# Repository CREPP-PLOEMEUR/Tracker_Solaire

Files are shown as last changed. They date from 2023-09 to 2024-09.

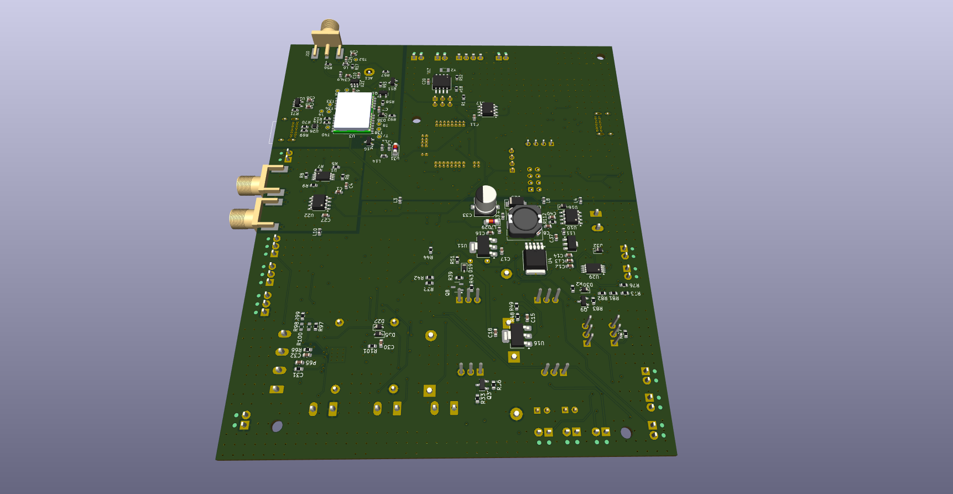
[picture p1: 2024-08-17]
Hardware/V2_CMS_4_Layers/Render/Bottom.png

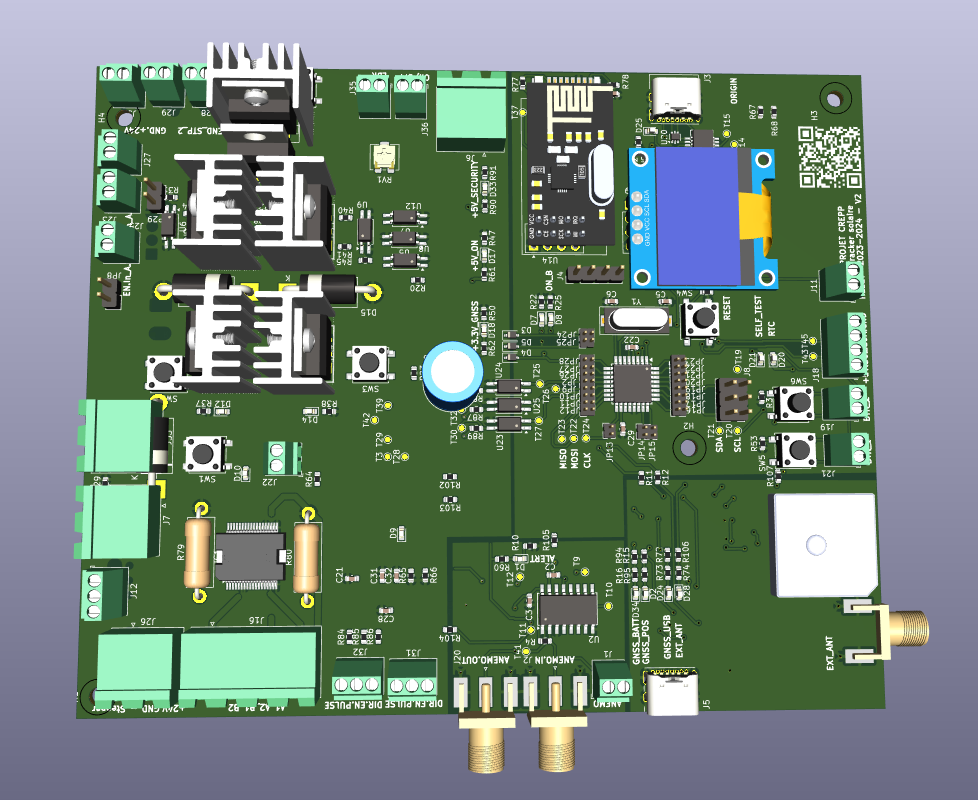
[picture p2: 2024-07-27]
Hardware/V2_CMS_4_Layers/img/img.png

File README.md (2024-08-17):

<!--# Tracker solaire -->
<!--+ 2023-2024 -->
<!--$ C++-->
<!--$ Freecad -->
<!--$ GPS -->
<!--% Ce projet vise à concevoir et construire un système de suivi solaire spécialement conçu pour maximiser l'efficacité de la capture d'énergie solaire à partir d'un panneau solaire. -->
 -->
# Projet de Tracker Solaire pour Panneau 1m x 1m60

Ce projet vise à concevoir et construire un système de suivi solaire spécialement conçu pour maximiser l'efficacité de la capture d'énergie solaire à partir d'un panneau solaire de dimensions spécifiques.

## Table des matières

- [Aperçu](#aperçu)
- [Fonctionnalités](#fonctionnalités)
- [Matériaux](#matériaux)
- [Schémas et Conception](#schémas-et-conception)

## Aperçu

Ce projet a pour objectif de créer un tracker solaire qui ajuste automatiquement la position d'un panneau solaire de 1 mètre sur 1 mètre 60 pour suivre le mouvement du soleil tout au long de la journée. Cette optimisation permettra une captation maximale de l'énergie solaire disponible.

## Fonctionnalités

Le tracker solaire comprend différentes fonctionnalités :

- Suivi précis et automatique de la trajectoire du soleil pour maximiser la production d'énergie solaire.
- Utilisation d'un module GPS pour déterminer la position du panneau solaire.  Une fois la position captée, l'heure permet de calculer 
la position du Soleil à n'importe quel moment de la journée.
- Un module RTC (Real Time Clock) enregistre l'heure pour éviter de solliciter le module GPS
- Contrôle fluide des moteurs pour ajuster la position du panneau solaire 
- Interface de communication pour surveiller et configurer les performances du tracker.
- Tous les évènements sont enregistrés dans une carte microSD.
- Le tracker se met en veille profonde dès que la luminosité devient trop faible.
- Une rafale de vent, dont la consigne peut être ajustée par l'utilisateur, réveille en cas de besoin le tracker pour le mettre en position horizontale.

## Matériaux

- Composants électroniques standard tels que microcontrôleurs, GPS, moteurs pas à pas, etc.
- Carte de circuit imprimé spécialement conçue pour le tracker solaire.

Image de PCB

- Moteurs pas à pas robustes adaptés aux dimensions du panneau solaire.
- Structure mécanique pour soutenir et orienter le panneau solaire.
- Source d'alimentation adaptée aux moteurs et à l'électronique.

## Schémas et Conception

Les schémas électriques détaillés et les plans de conception du circuit imprimé spécifique au tracker solaire sont disponibles dans le dossier `Hardware`.

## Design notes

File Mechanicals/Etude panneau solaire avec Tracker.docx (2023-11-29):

Etude panneau solaire Terre avec Tracker

Hypothèse de départ :

- Puissance visée dans condition optimum : 400w
- Alimente une batterie dont les caractéristiques seront à déterminer en fonction de l’usage
- Données latitude 48° N (voir graphique ci-après)
- Rotation max azimut retenue : -100° vers l’est et + 100° vers l’ouest
- Rotation max hauteur par rapport au zénith (0°) : de 10° à 70°
- Protection des vents fort (> à 60 km/h) par mise à plat du panneau et orientation par rapport au vent dans la limite de l’azimut
- Hauteur maxi de l’ensemble 1800 mm pour pouvoir l’installer sans demande de travaux
- Cout maximum (pièces uniquement) : 600€
- Tenue mécanique de l’ensemble calculé avec 10° par rapport au zénith et azimut axe du vent pour vent de 100 km/h max
- Protection corrosion : choix des matériaux pour minimum d’entretien
- Protection poussière/humidité : IP64
- Mise en mouvement : utilisation de solutions que l’on peut trouver facilement dans le commerce avec prix raisonnables (moteurs – vérins électriques)
- Mécanisme optimisé au niveau des frottements pour minimiser la consommation de mise en mouvement (inertie de mise en œuvre du mouvement non pris en compte)
- Fréquence de mise en mouvement à adapter à la vitesse de rotation de la terre par rapport au soleil : tous les 4/5° par exemple => voir si on différencie pour les saisons

Autres données :

- Gain tracker 2 axes : 40% => multiples sources internet
- Gain tracker 1 axe : 25% => multiples sources internet

Les composants de l’installation :

- Panneau solaire adaptable sur châssis (1700x1100mm)
- Transformateur de courant
- Centrale et capteur du tracker (à détailler)
- Anémomètre (vitesse et direction du vent)
- Batterie de stokage
- Châssis fixe (profilés, roulements, axes, vis,…)
- Châssis mobile (profilés, roulements, axes, vis,…)
- Réducteur roue/vis sans fin pour déplacement azimut +100° _ -100° : 1 tour moteur = 4°
- Moteur NEMA 23
- Vérin hauteur
- Câbles

Annexe 1

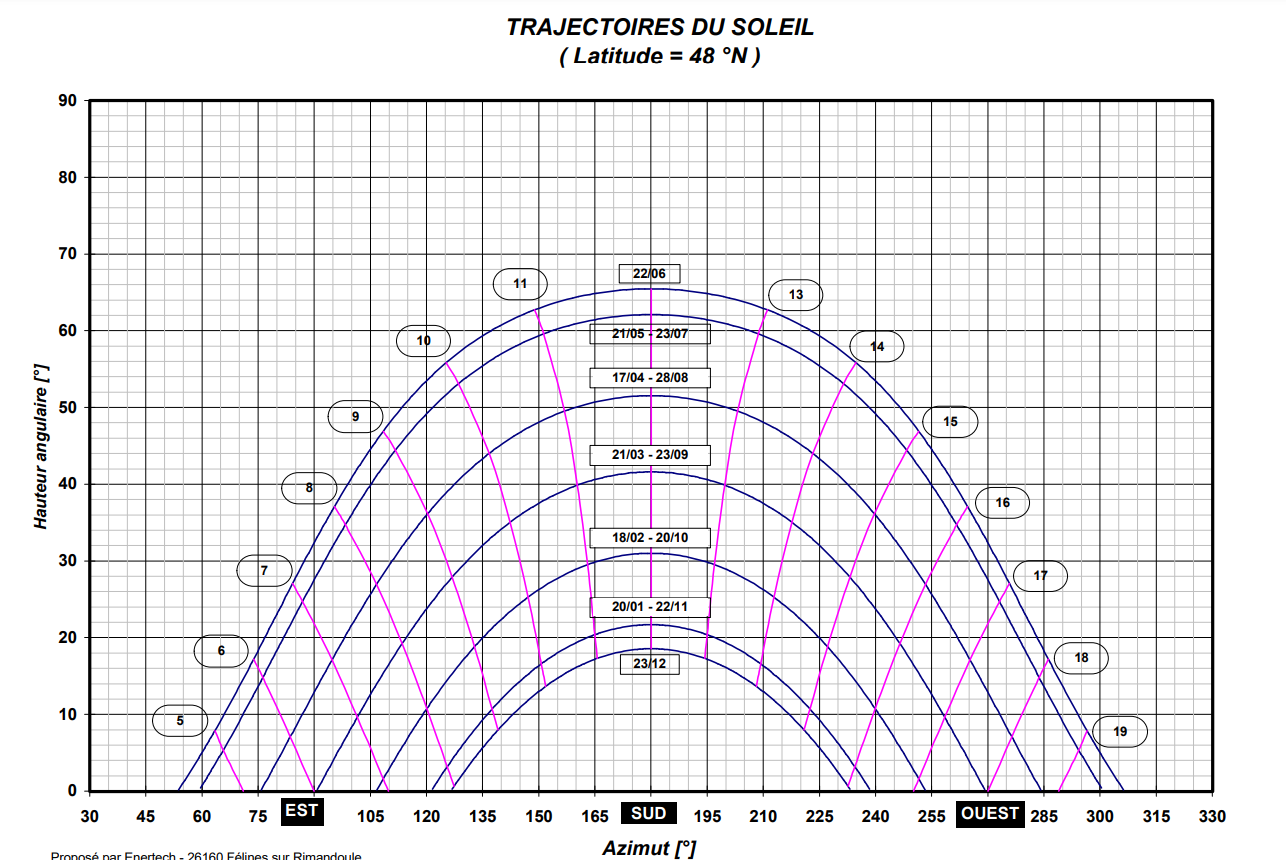
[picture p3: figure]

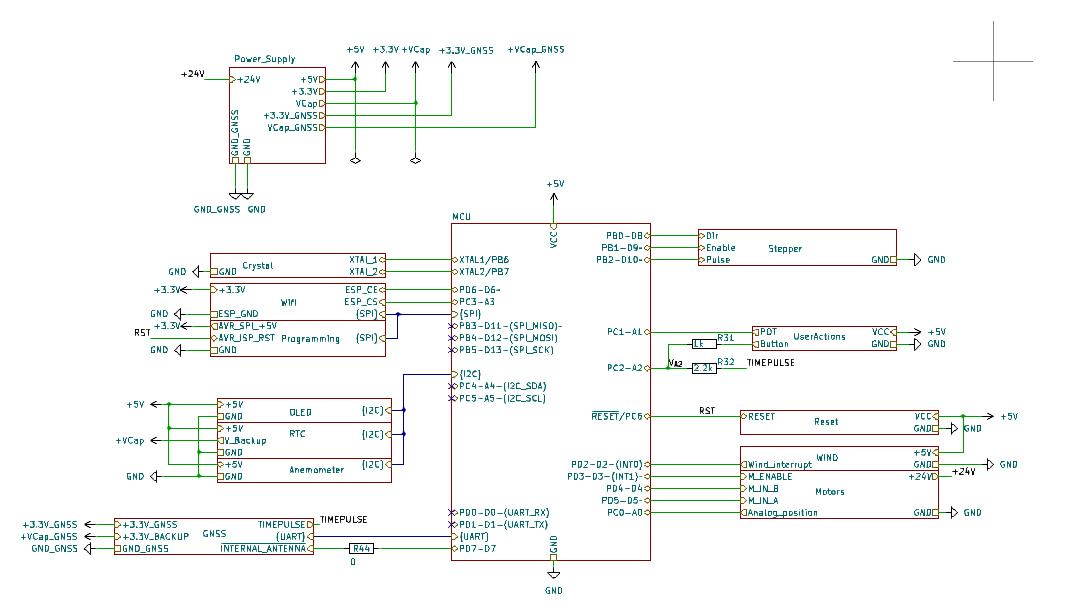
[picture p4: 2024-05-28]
Images/SCHEMATIC.png

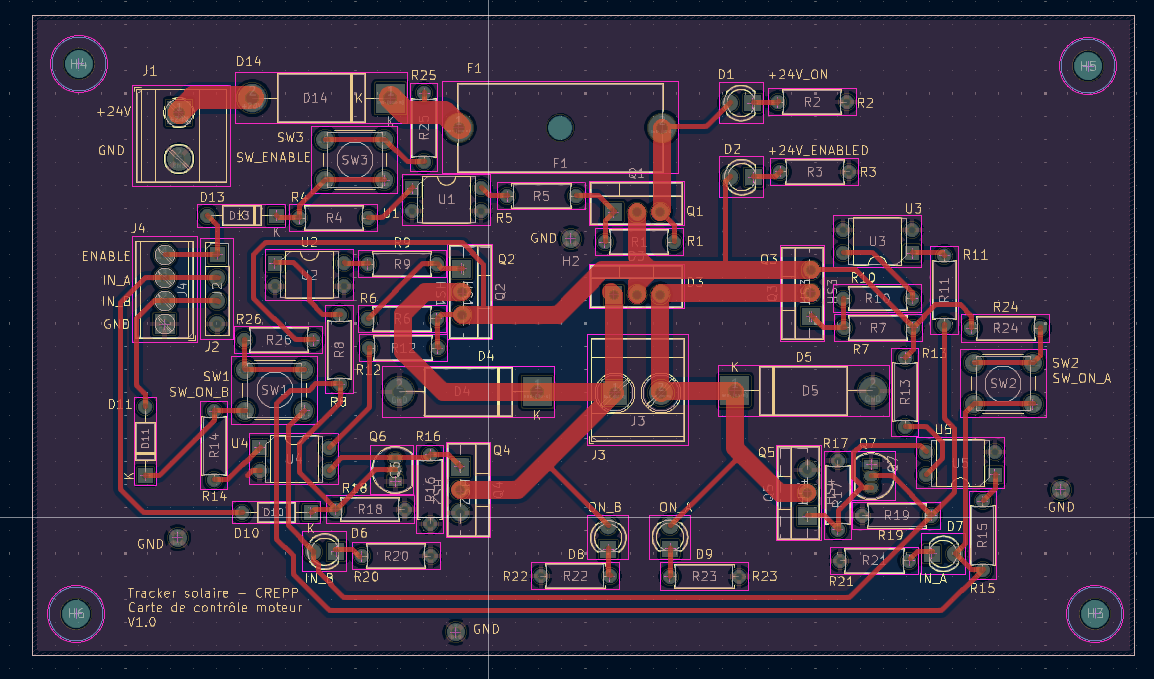
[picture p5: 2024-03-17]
Hardware/V1_THT/Submodules/Motor_Control/Render/Routage.png

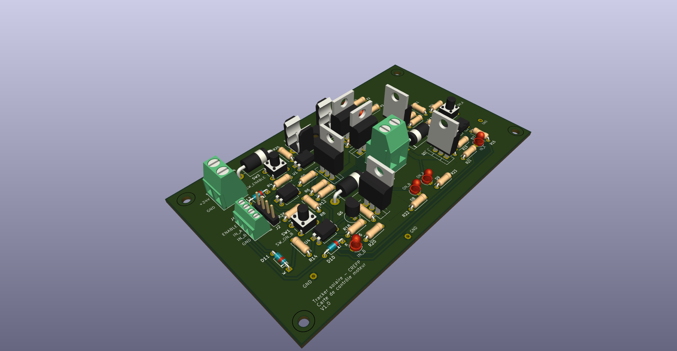
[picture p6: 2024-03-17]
Hardware/V1_THT/Submodules/Motor_Control/Render/Top_empty_45.png

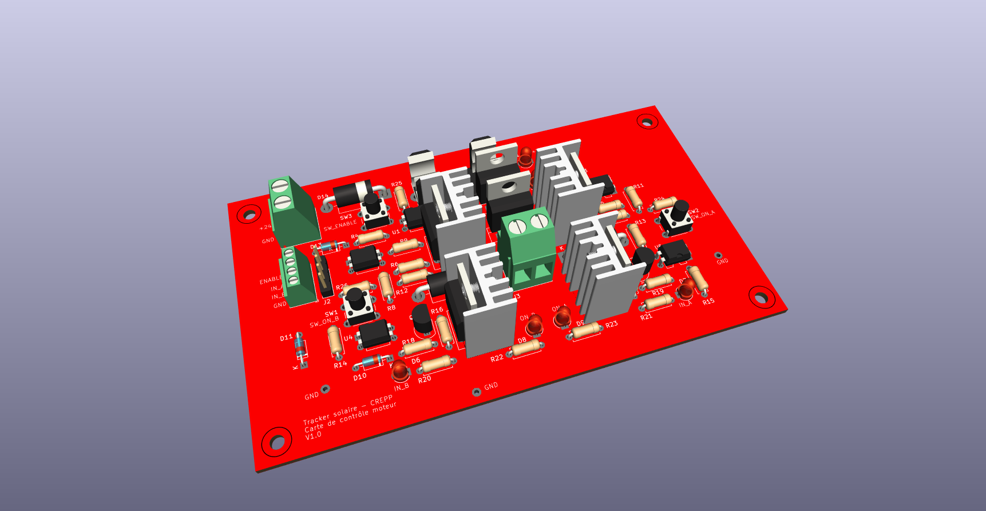
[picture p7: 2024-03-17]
Hardware/V1_THT/Submodules/Motor_Control/Render/Motor_Control.png

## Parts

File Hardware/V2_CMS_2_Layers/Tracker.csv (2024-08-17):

Id | Référence | Empreinte | Quantité | Désignation | Fournisseur et réf
1 | R10 | R_0603_1608Metric | 1 | R_330R_SMD_0603
2 | D20,D10,D18,D9,D12,D1,D17,D14,D7,D33,D21,D8 | LED_0603_1608Metric | 12 | LED
3 | R53,R97,R46,R4,R78,R3,R77,R110,R64,R76,R81,R101,R99,R83,R82,R75,R100,R57 | R_0603_1608Metric | 18 | 10k
4 | J27 | TerminalBlock_Phoenix_MPT-0,5-2-2.54_1x02_P2.54mm_Horizontal | 1 | EN_LED
5 | T10,T41,T44,T31,T42,T17,T51,T26,T9,T28,T50,T45,T36,T16,T30,T22,T35,T46,T32,T37,T29,T24,T14,T25,T43,T11,T20,T15,T3,T23,T21,T27,T12,T19,T18,T8,T1,T40,T5,T34,T38,T33,T7,T4,T52 | TestPoint_Pad_D1.0mm | 45 | TP
6 | R88,R87,R86,R89,R84,R85 | R_0603_1608Metric | 6 | 220
7 | R19,R54,R25,R22,R55 | R_0603_1608Metric | 5 | 270
8 | J20,J2,J10 | SMA_Molex_73251-1153_EdgeMount_Horizontal | 3 | 132415
9 | D2 | LED_0603_1608Metric | 1 | POS_ENABLE
10 | JP10,JP23,JP19,JP9,JP28,JP18,JP1,JP27,JP3,JP14,JP22,JP20,JP2,JP24,JP11,JP12,JP25,JP21,JP13,JP26,JP17,JP15,JP16 | PinHeader_1x02_P1.27mm_Vertical | 23 | Jumper_2_Open
11 | HS2,HS4,HS3,HS1,HS5 | HeastSink_MOSFET_15mm_10mm_20mm | 5 | Heatsink
12 | SW3,SW4,SW7,SW2 | SW_Push_1P1T_NO_CK_KSC7xxJ | 4 | PB_SMD_12V_50MA_6MM_6MM
13 | U6,U5,U9,U25,U7,U23,U8,U24 | SOP-4_4.4x2.6mm_P1.27mm | 8 | PC817XI
14 | U18 | SSOP-14_5.3x6.2mm_P0.65mm | 1 | LVC125A
15 | J26,J6 | PhoenixContact_MSTBA_2,5_2-G-5,08_1x02_P5.08mm_Horizontal | 2 | +24V
16 | R16,R91,R73,R47,R50,R74,R95,R52,R1 | R_0603_1608Metric | 9 | 330
17 | J4 | PinHeader_1x04_P2.54mm_Vertical | 1 | PinHeader_Control
18 | D24 | LED_0603_1608Metric | 1 | GNSS_USB
19 | J37 | microSD_HC_Hirose_DM3D-SF | 1 | Micro_SD_Card
20 | R38,R26,R37,R29,R63 | R_0603_1608Metric | 5 | 3.3K
21 | SW5,SW6 | SW_Push_1P1T_NO_CK_KSC7xxJ | 2 | SW_User
22 | J21,J36,J35,J23,J19,J25,J29,J22,J11,J30,J28 | TerminalBlock_Phoenix_MPT-0,5-2-2.54_1x02_P2.54mm_Horizontal | 11 | KF128-2.54_2P
23 | R40,R35,R42,R32 | R_0603_1608Metric | 4 | 1K
24 | D4,D5,D3,D30,D36,D22,D32,D35 | D_SOD-323 | 8 | 1N4148
25 | R67,R62,R15,R12,R68,R60,R107,R94,R106,R90,R102,R11,R72,R103,R61,R69,R18,R70,R71,R2 | R_0603_1608Metric | 20 | 0
26 | C38,C24,C3,C21,C41,C39,C23,C22,C2,C29,C8,C4,C14,C27,C12,C1,C37,C7,C15,C30,C36,C11,C16,C20,C18,C17 | C_0603_1608Metric | 26 | 100nF
27 | R34,R28,R41 | R_0603_1608Metric | 3 | 2.2K
28 | D6,D15,D11 | D_DO-201AD_P15.24mm_Horizontal | 3 | 1N5408
29 | D27 | LED_0603_1608Metric | 1 | RX_LED
30 | IC1 | ST_PowerSSO-36_SlugDown_ThermalVias | 1 | L6208
31 | SW1 | SW_Push_1P1T_NO_CK_KSC7xxJ | 1 | SW_E
32 | R59,R96,R112,R27,R33,R13,R43,R14,R58 | R_0603_1608Metric | 9 | 1k
33 | U14 | nRF24L01_Breakout | 1 | NRF24L01_Breakout
34 | C19 | C_Radial_D10.0mm_H20.0mm_P5.00mm | 1 | 20F
35 | R108,R109 | R_0603_1608Metric | 2 | 4.7k
36 | U15 | TQFP-32_7x7mm_P0.8mm | 1 | ATMEGA-328P
37 | Q5,Q7 | TO-220-3_Vertical | 2 | IRF520
38 | R23,R31,R45,R30,R44 | R_0603_1608Metric | 5 | 470
39 | RV2 | Potentiometer_Bourns_3314S_Horizontal | 1 | Vref_B
40 | Y1 | Crystal_SMD_HC49-SD | 1 | 16MHz
41 | C6,C5 | C_0603_1608Metric | 2 | 22pF
42 | R80,R79 | R_Axial_DIN0414_L11.9mm_D4.5mm_P15.24mm_Horizontal | 2 | 0.33
43 | JP8,JP29 | PinHeader_1x02_P2.54mm_Vertical | 2 | Jumper
44 | U20,U26 | SOT-666 | 2 | USBLC6-2P6
45 | H3,H4,H1,H2 | MountingHole_3mm | 4 | MountingHole
46 | U28 | TSSOP-10_3x3mm_P0.5mm | 1 | ADS1115IDGS
47 | R24,R21,R20 | R_0603_1608Metric | 3 | 2.7k
48 | J8 | PinHeader_2x03_P2.54mm_Vertical | 1 | I2C_Selector
49 | Q6,Q2,Q4 | TO-220-3_Vertical | 3 | IRF4905
50 | C28 | C_0603_1608Metric | 1 | 4.7u
51 | D25 | LED_0603_1608Metric | 1 | LED_USB
52 | J18 | TerminalBlock_Phoenix_MPT-0,5-4-2.54_1x04_P2.54mm_Horizontal | 1 | KF128-2.54_4P
53 | R104,R105 | R_0603_1608Metric | 2 | R_0R_SMD_0603
54 | J33 | PhoenixContact_MSTBA_2,5_2-G-5,08_1x02_P5.08mm_Horizontal | 1 | Fuse
55 | J32,J12 | TerminalBlock_Phoenix_MPT-0,5-3-2.54_1x03_P2.54mm_Horizontal | 2 | KF128-2.54_3P
56 | RV3 | Potentiometer_Bourns_3314S_Horizontal | 1 | Vref_A
57 | J7 | PhoenixContact_MSTBA_2,5_2-G-5,08_1x02_P5.08mm_Horizontal | 1 | Motor
58 | J3,J5 | USB_C_Receptacle_GCT_USB4085 | 2 | USB_C_Receptacle_USB2.0_16P
59 | D13 | TO-220-3_Vertical | 1 | D_Dual_CommonCathode_AAK
60 | J1 | TerminalBlock_Phoenix_MPT-0,5-2-2.54_1x02_P2.54mm_Horizontal | 1 | Wind
61 | U2 | SOIC-16W_5.3x10.2mm_P1.27mm | 1 | 74HC123D
62 | D28 | LED_0603_1608Metric | 1 | LED_EXT_ANTENNA
63 | D26 | LED_0603_1608Metric | 1 | TX_LED
64 | RV1 | Potentiometer_Bourns_3314S_Horizontal | 1 | Light_Reference
65 | J9 | PinSocket_1x04_P2.54mm_Vertical | 1 | OLED_SOCKET
66 | J31 | TerminalBlock_Phoenix_MPT-0,5-3-2.54_1x03_P2.54mm_Horizontal | 1 | Motor_Control_Pull_Up
67 | D34 | LED_0603_1608Metric | 1 | GNSS_BATT
68 | J16 | PhoenixContact_MSTBA_2,5_4-G-5,08_1x04_P5.08mm_Horizontal | 1 | Stepper
69 | U19 | SSOP-20_3.9x8.7mm_P0.635mm | 1 | FT231XS
70 | L12 | L_0603_1608Metric | 1 | MPZ1608
71 | L2,L1,L3,L11,L8,L10,L4,L14,L13,L7 | L_0603_1608Metric | 10 | MPZ1608S101ATAH0
72 | U22 | SOIC-8_3.9x4.9mm_P1.27mm | 1 | MCP4011
73 | R8,R9,R7,R5,R6 | R_0603_1608Metric | 5 | R_10K_SMD_0603
74 | C34,C9,C10 | C_0603_1608Metric | 3 | 120pF
75 | U21 | SOT-23-6 | 1 | AS193-73LF
76 | R17 | R_0603_1608Metric | 1 | R_680K_SMD_0603
77 | C33 | CP_Elec_6.3x7.7 | 1 | 220uF
78 | D31 | D_MiniMELF | 1 | ZENER_3.6V
79 | U29,U1 | TSSOP-8_4.4x3mm_P0.65mm | 2 | LM358DR
80 | U11 | SOT-223-3_TabPin2 | 1 | AMS1117-3.3
81 | Q10 | SOT-23 | 1 | CJ3401
82 | R51,R49,R48 | R_0603_1608Metric | 3 | 100
83 | R66,R65 | R_0603_1608Metric | 2 | XX
84 | U4 | TO-252-5_TabPin3 | 1 | XL1507
85 | R39,R36,R56 | R_0603_1608Metric | 3 | 100k
86 | C31,C32 | C_0603_1608Metric | 2 | XX
87 | C25,C26 | C_0603_1608Metric | 2 | 330pF
88 | D23 | D_SMA | 1 | SS34
89 | L6 | L_0603_1608Metric | 1 | 56nH
90 | D19,D16 | D_SOD-323 | 2 | 1N4818
91 | U16 | SOT-223-3_TabPin2 | 1 | LM317DCYG3
92 | U17 | SOIC-8_3.9x4.9mm_P1.27mm | 1 | PCA9536D
93 | C40,C35 | C_0603_1608Metric | 2 | 1nF
94 | Q8,Q3 | SOT-23-3 | 2 | 2N7000
95 | Y2 | Crystal_SMD_3215-2Pin_3.2x1.5mm | 1 | 32kHz
96 | L9 | L_0603_1608Metric | 1 | 39nH
97 | AE1 | MountingHole_2.2mm_M2_DIN965_Pad | 1 | Internal_antenna
98 | U12 | SOT-89-3 | 1 | MC78L05_SOT89
99 | U13 | SO-8_5.3x6.2mm_P1.27mm | 1 | DS1307Z
100 | Q9,Q11 | SOT-23 | 2 | 2N7002
101 | U3 | ublox_NEO | 1 | NEO-M8M
102 | R92 | R_0603_1608Metric | 1 | R_100K_SMD_0603
103 | D29 | D_MiniMELF | 1 | ZENER_5.6V
104 | U10 | SOIC-8_3.9x4.9mm_P1.27mm | 1 | ACS712xLCTR-05B
105 | L5 | L_Wuerth_HCI-5040 | 1 | 33nH
106 | R93 | R_0603_1608Metric | 1 | R_1K_SMD_0603
107 | C13 | C_0603_1608Metric | 1 | 22uF
108 | Q1 | SOT-23 | 1 | SI2302
109 | U27 | SOT-23-5 | 1 | LP2985-3.3

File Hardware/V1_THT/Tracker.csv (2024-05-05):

Id | Référence | Empreinte | Quantité | Désignation | Fournisseur et réf
1 | JP8,JP4,JP5,JP2,JP6,J16,J17,JP3,JP1,JP7 | PinHeader_1x02_P2.54mm_Vertical | 10 | Jumper
2 | F1 | Fuseholder_Cylinder-5x20mm_Schurter_0031_8201_Horizontal_Open | 1 | Fuse
3 | R43,R42,R6,R40,R4,R6,R5,R4,R7,R5,R41,R7,R8,R8 | R_Axial_DIN0207_L6.3mm_D2.5mm_P7.62mm_Horizontal | 14 | 10k
4 | U7,U9,U11,U8,U10 | DIP-4_W7.62mm | 5 | PC817
5 | J1,J1,J1 | TerminalBlock_Phoenix_MKDS-1,5-2-5.08_1x02_P5.08mm_Horizontal | 3 | Battery
6 | H2,H3,H2,H6,H1,H4,H4,H7,H3,H5,H1,H8,H1 | MountingHole_3mm | 13 | MountingHole
7 | D1,D1,D3,D4,D1,D3 | D_DO-41_SOD81_P7.62mm_Horizontal | 6 | 1N4818
8 | J6 | TerminalBlock_Phoenix_MKDS-1,5-2-5.08_1x02_P5.08mm_Horizontal | 1 | END_STOP_1
9 | J8,J8 | PinHeader_2x05_P2.54mm_Vertical | 2 | SPI_Programming
10 | J4,J4,J3,J4,J5,J5,J3 | PinHeader_1x01_P2.54mm_Vertical | 7 | GND
11 | R10 | R_Axial_DIN0207_L6.3mm_D2.5mm_P7.62mm_Horizontal | 1 | 330
12 | R23,R20,R31,R32 | R_Axial_DIN0207_L6.3mm_D2.5mm_P7.62mm_Horizontal | 4 | 3.3K
13 | D9,D12,D14,D10,D2,D2,D11,D16 | LED_D3.0mm | 8 | LED
14 | U1,U1,U1 | TO-220-3_Vertical | 3 | L7805
15 | R38,R24,R39,R25,R17 | R_Axial_DIN0207_L6.3mm_D2.5mm_P7.62mm_Horizontal | 5 | 470
16 | C7,C8 | C_Disc_D4.7mm_W2.5mm_P5.00mm | 2 | 22pF
17 | R12,R21,R12,R13,R21 | R_Axial_DIN0207_L6.3mm_D2.5mm_P7.62mm_Horizontal | 5 | 1k
18 | Q4,Q6 | TO-220-3_Vertical | 2 | IRF520
19 | HS4,HS2,HS3,HS1 | HeastSink_MOSFET_15mm_10mm_20mm | 4 | Heatsink
20 | R26,R34,R36,R29 | R_Axial_DIN0207_L6.3mm_D2.5mm_P7.62mm_Horizontal | 4 | 1K
21 | R27,R37,R30,R33 | R_Axial_DIN0207_L6.3mm_D2.5mm_P7.62mm_Horizontal | 4 | 100k
22 | J7,J7 | TerminalBlock_Phoenix_MKDS-1,5-2-5.08_1x02_P5.08mm_Horizontal | 2 | END_STOP_2
23 | R16,R19,R1,R1,R16,R1 | R_Axial_DIN0207_L6.3mm_D2.5mm_P7.62mm_Horizontal | 6 | 270
24 | R11 | R_Axial_DIN0207_L6.3mm_D2.5mm_P7.62mm_Horizontal | 1 | 100
25 | J11 | PinHeader_1x04_P2.54mm_Vertical | 1 | PinHeader_Control
26 | D5,D7,D7,D6 | D_DO-35_SOD27_P7.62mm_Horizontal | 4 | 1N4148
27 | Q7,Q2 | TO-92_Inline | 2 | 2N7000
28 | U3,U3 | DIP-8_W7.62mm_Socket | 2 | LM358
29 | J13 | TerminalBlock_Phoenix_MKDS-1,5-2-5.08_1x02_P5.08mm_Horizontal | 1 | +24V
30 | J2,J2 | PinHeader_2x01_P2.54mm_Vertical | 2 | Haeder_LED
31 | D17,D8,D13 | D_DO-201AD_P15.24mm_Horizontal | 3 | 1N5408
32 | SW2 | SW_PUSH_6mm_H8mm | 1 | SW_E
33 | C5,C9,C10,C6,C3,C3,C4 | C_Rect_L7.0mm_W2.0mm_P5.00mm | 7 | 100nF
34 | C1,C1 | C_Rect_L7.0mm_W2.0mm_P5.00mm | 2 | 1nF
35 | R14,R18,R15 | R_Axial_DIN0207_L6.3mm_D2.5mm_P7.62mm_Horizontal | 3 | 2.7k
36 | D15 | TO-220-3_Vertical | 1 | D_Dual_CommonCathode_AAK
37 | R28,R35,R22 | R_Axial_DIN0207_L6.3mm_D2.5mm_P7.62mm_Horizontal | 3 | 2.2K
38 | U4 | DIP-16_W7.62mm_Socket | 1 | 74HC123
39 | Q5,Q1,Q3 | TO-220-3_Vertical | 3 | IRF4905
40 | J12 | PinHeader_1x01_P2.54mm_Vertical | 1 | Analog_Position
41 | R3,R3,R3 | R_Axial_DIN0207_L6.3mm_D2.5mm_P7.62mm_Horizontal | 3 | 470k
42 | C2,C2 | C_Radial_D5.0mm_H11.0mm_P2.00mm | 2 | 4.7uF
43 | J10 | SMA_Molex_73251-1153_EdgeMount_Horizontal | 1 | 132134
44 | C11 | C_Radial_D10.0mm_H20.0mm_P5.00mm | 1 | 20F
45 | J14 | TerminalBlock_Phoenix_MKDS-3-2-5.08_1x02_P5.08mm_Horizontal | 1 | Motor
46 | R9,R9 | R_Axial_DIN0207_L6.3mm_D2.5mm_P7.62mm_Horizontal | 2 | 220
47 | RV1 | Potentiometer_Bourns_3266Y_Vertical | 1 | R_Potentiometer
48 | U2,U2 | DIP-28_W7.62mm | 2 | ATmega328P-P
49 | SW3 | SW_PUSH_6mm_H8mm | 1 | SW_B
50 | SW5 | SW_PUSH_6mm | 1 | SW_Push
51 | U6 | ublox_NEO | 1 | GK9501
52 | Y1 | Crystal_HC49-4H_Vertical | 1 | 16MHz
53 | J9 | TerminalBlock_Phoenix_MKDS-1,5-2-5.08_1x02_P5.08mm_Horizontal | 1 | Wind
54 | U5 | TO-220-3_Vertical | 1 | LM317_TO-220
55 | SW4 | SW_PUSH_6mm_H8mm | 1 | SW_A

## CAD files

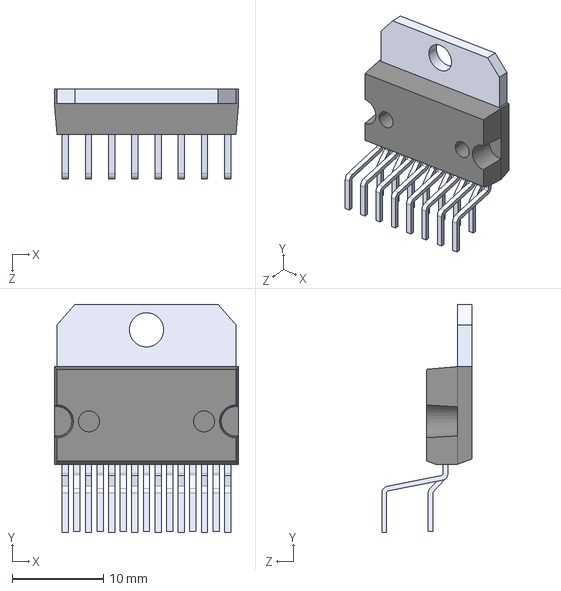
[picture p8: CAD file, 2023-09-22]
Hardware/V2_CMS_2_Layers/Kicad_3D/E-L298N.STEP
20.2 x 25.0 x 9.89 mm

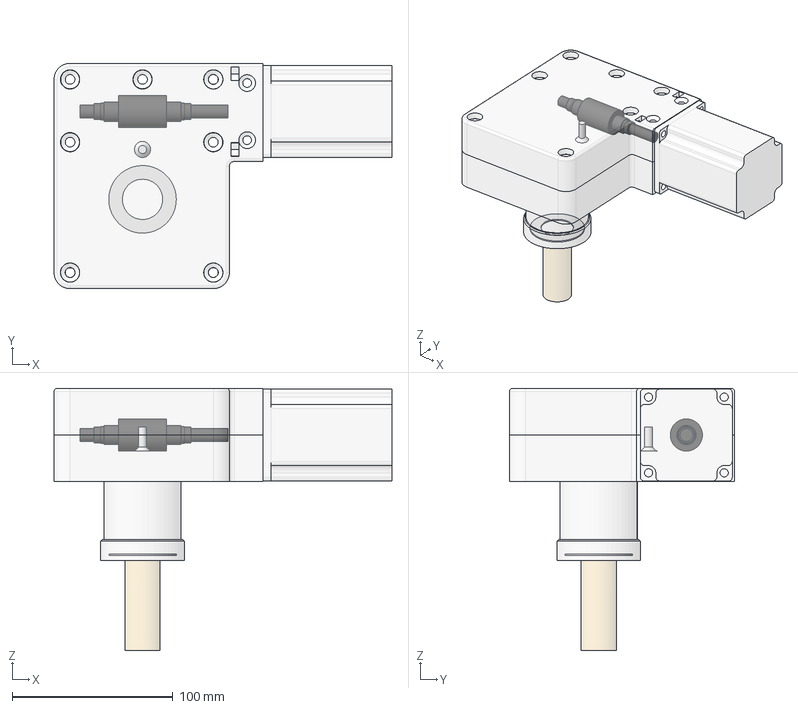
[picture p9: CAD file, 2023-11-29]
Mechanicals/Freecad/réducteur-roue-vis_sans_fin_54.FCStd
210.0 x 140.0 x 163.0 mm
couronne
Vis_sans_fin
roulement_8_12_10_1
roulement_8_12_10_2
butée_aiguille_10_24_6-1
butée_aiguille_10_24_6_2
accouplement
tube
axe
moteur_nema_23
roulement_22x44x12
1/2 carter haut
1/2_carter_bas
roulement_15x35x11
vis M5x15
roulement_22x44x12_2
rondelle butée_aiguille
butee_aiguille_25x42x2_1
rondelle butée_aiguille001
entretoise_butée
cache_poussière

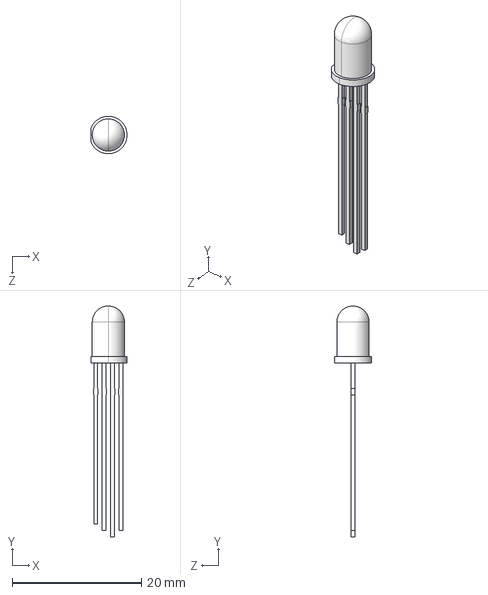
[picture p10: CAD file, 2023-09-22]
Hardware/V2_CMS_2_Layers/Kicad_3D/Led RGB 5mm.STEP
5.60 x 35.8 x 5.80 mm
Lente^Led RGB 5mm
Terminais^Led RGB 5mm

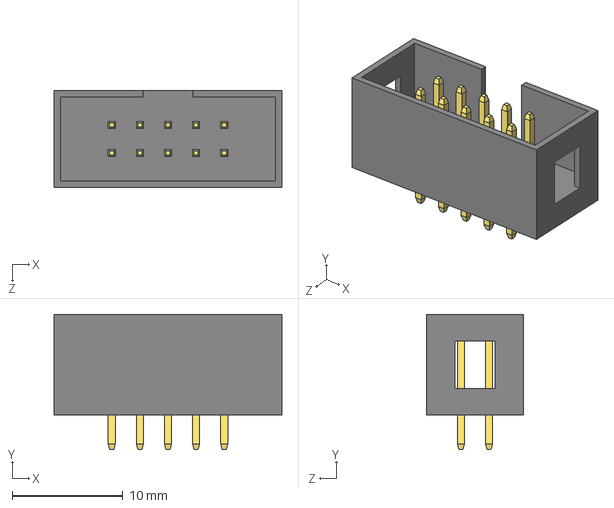
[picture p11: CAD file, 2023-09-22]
Hardware/V2_CMS_4_Layers/Kicad_3D/AVR_ISP_2R5W_254P.STEP
20.6 x 12.2 x 8.80 mm

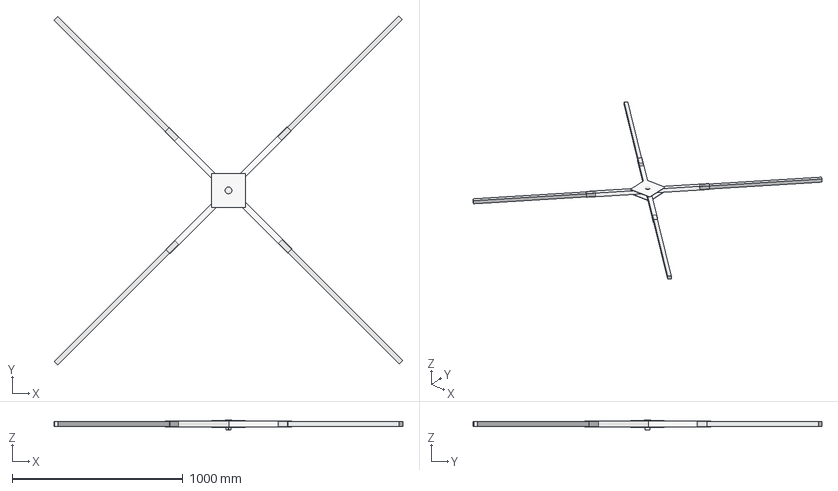
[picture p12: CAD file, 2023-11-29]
Mechanicals/Freecad/cadre_fixe.FCStd
2042.6 x 2044.3 x 60.0 mm
cadre
rallonge_cadre_fixe
rallonge_cadre_fixe001
rallonge_cadre_fixe002
rallonge_cadre_fixe003

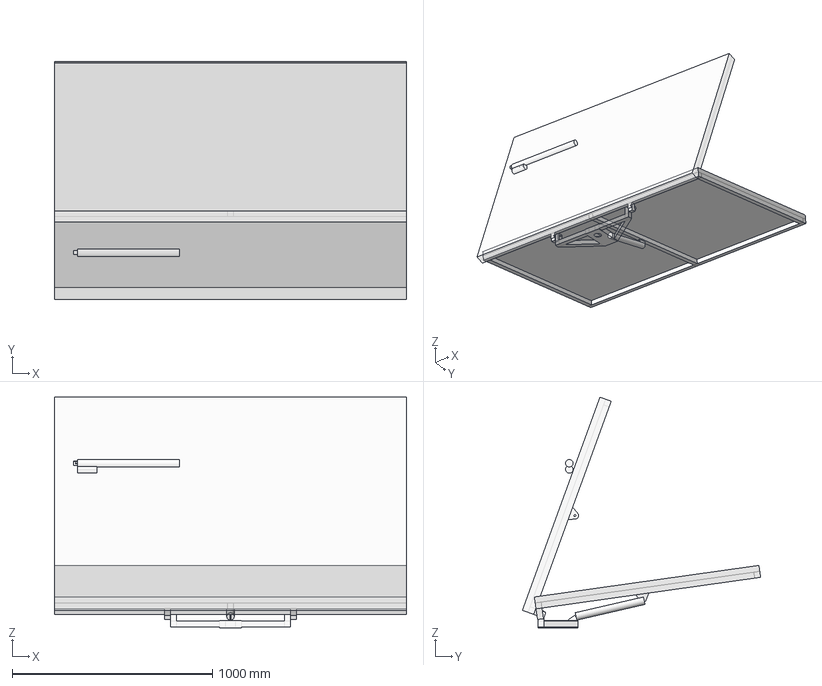
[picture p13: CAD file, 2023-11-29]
Mechanicals/Freecad/tracker_solaire.FCStd
1760.0 x 1191.2 x 1153.4 mm
Chassis_panneau_1760x1134_70°
chassis_mobile
verin_position_max_70°
verin_position_min_10°
Chassis_panneau_1760x1134_10°

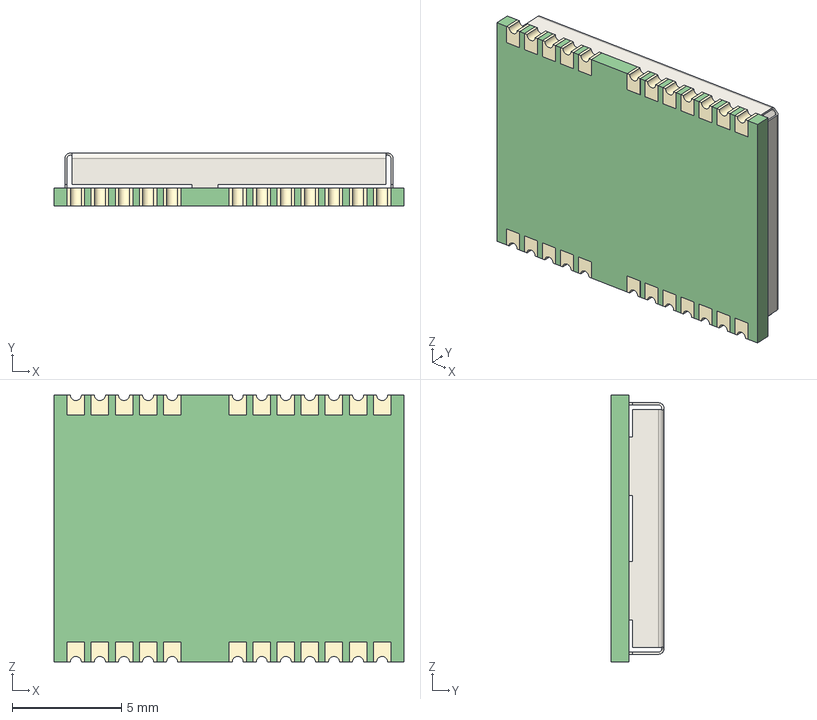
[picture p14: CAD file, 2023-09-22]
Hardware/V2_CMS_4_Layers/Kicad_3D/NEO-M8U.step
16.0 x 2.42 x 12.2 mm
Board
Solder pads

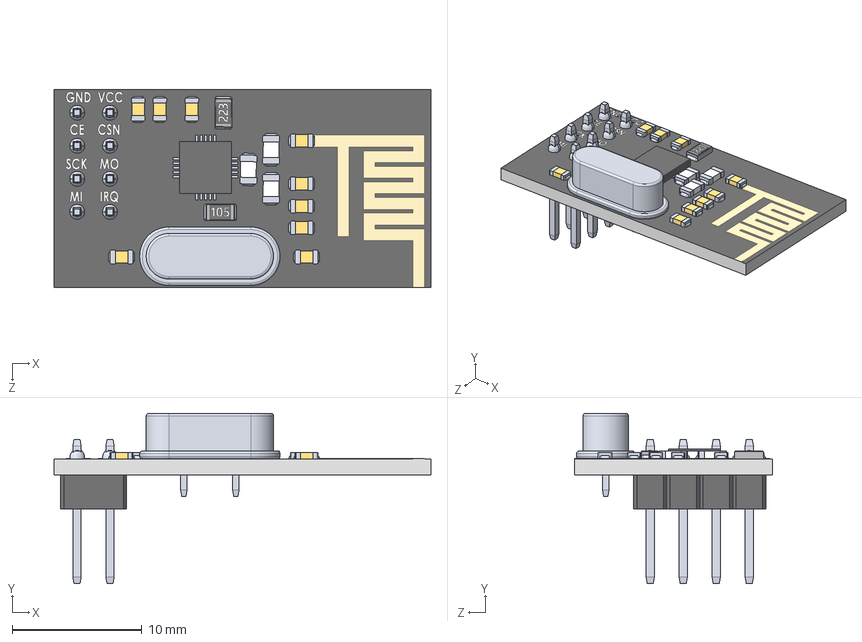
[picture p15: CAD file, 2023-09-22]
Hardware/V2_CMS_2_Layers/Kicad_3D/NRF24.STEP
29.0 x 13.1 x 15.2 mm
nrfboard
CrystalOscillator
doubleMaleHeader x 4
solder x 8
1.7mmSmdCeramicCapacitor x 9
smdResistor223
smdResistor105
smdceramiccapacitorwhite x 3
4x4SMDchip

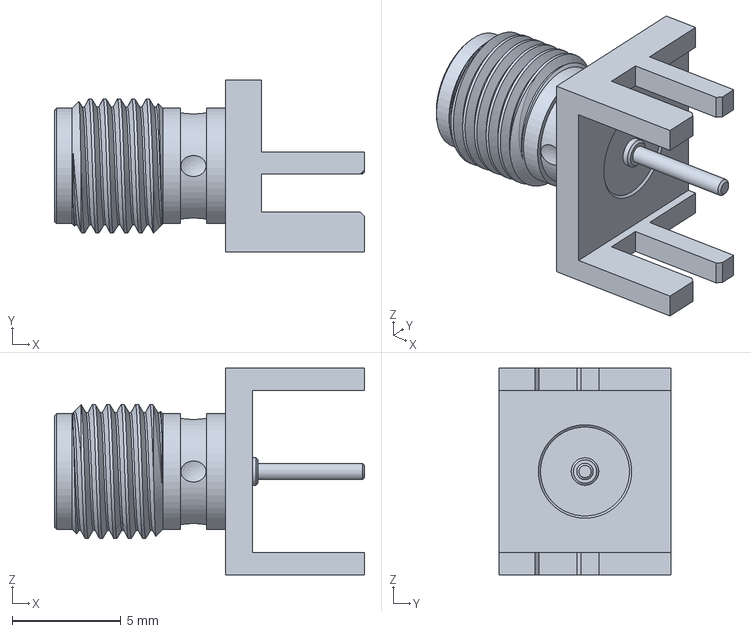
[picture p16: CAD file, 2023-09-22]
Hardware/V2_CMS_4_Layers/Kicad_3D/132255.stp
14.3 x 7.92 x 9.52 mm

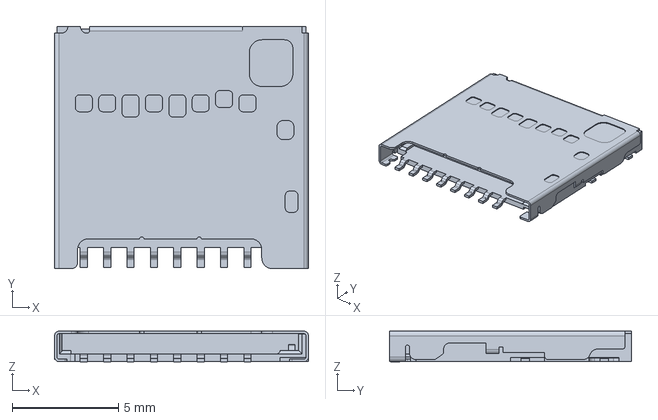
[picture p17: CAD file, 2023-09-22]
Hardware/V2_CMS_4_Layers/Kicad_3D/8967560.stp
11.9 x 11.4 x 1.45 mm

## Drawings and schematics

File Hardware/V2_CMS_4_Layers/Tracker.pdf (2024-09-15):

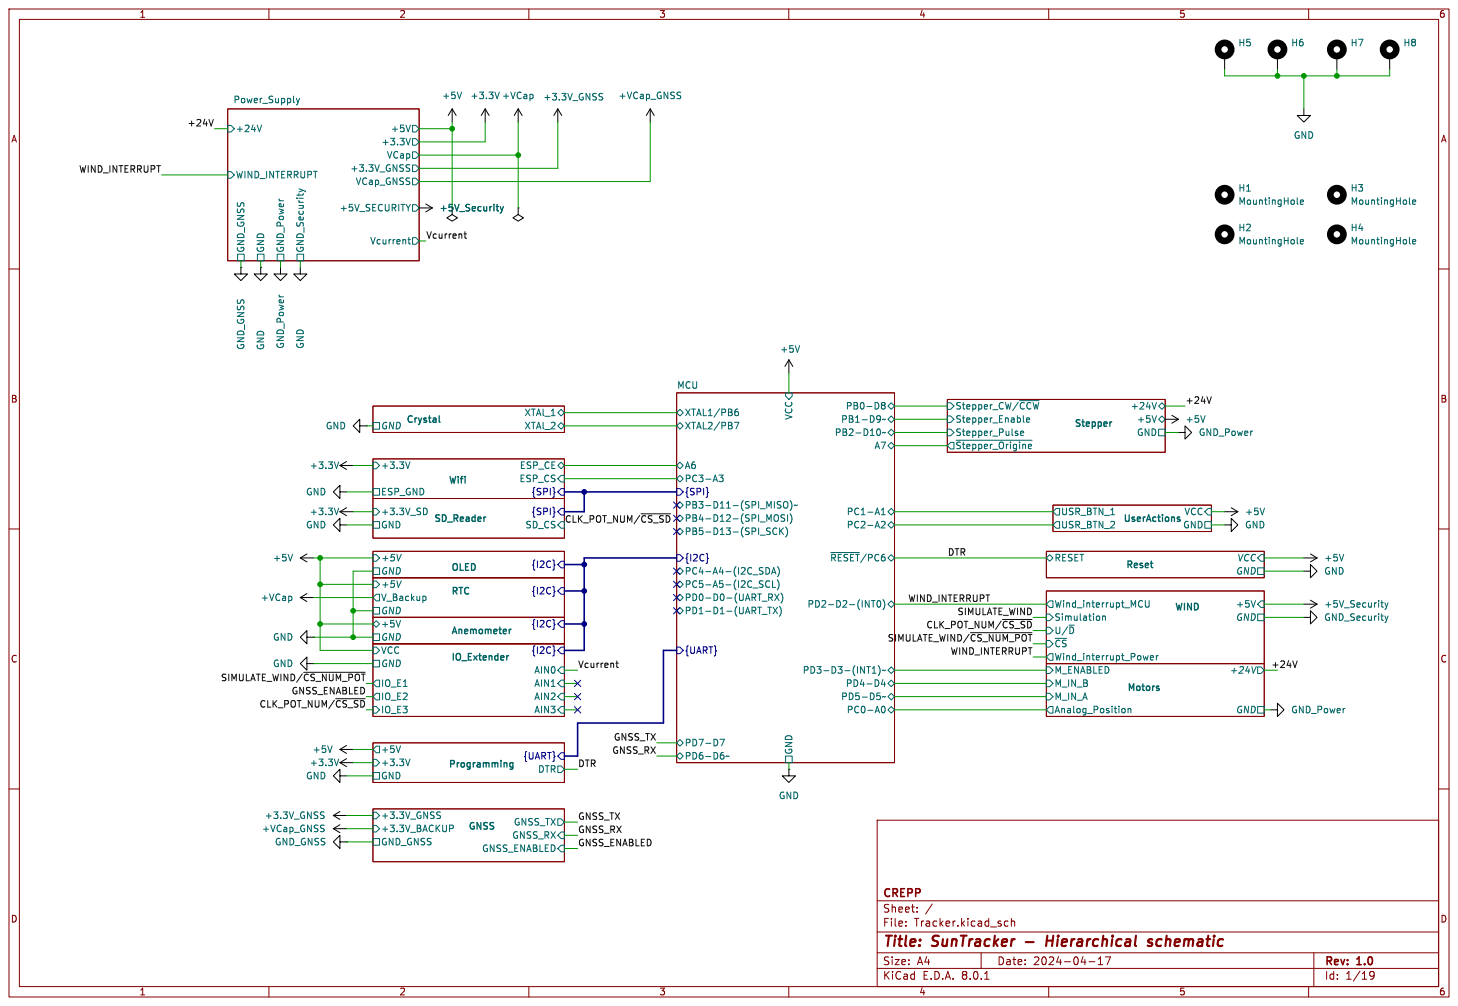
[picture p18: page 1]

File: Tracker.kicad_sch Sheet: / CREPP

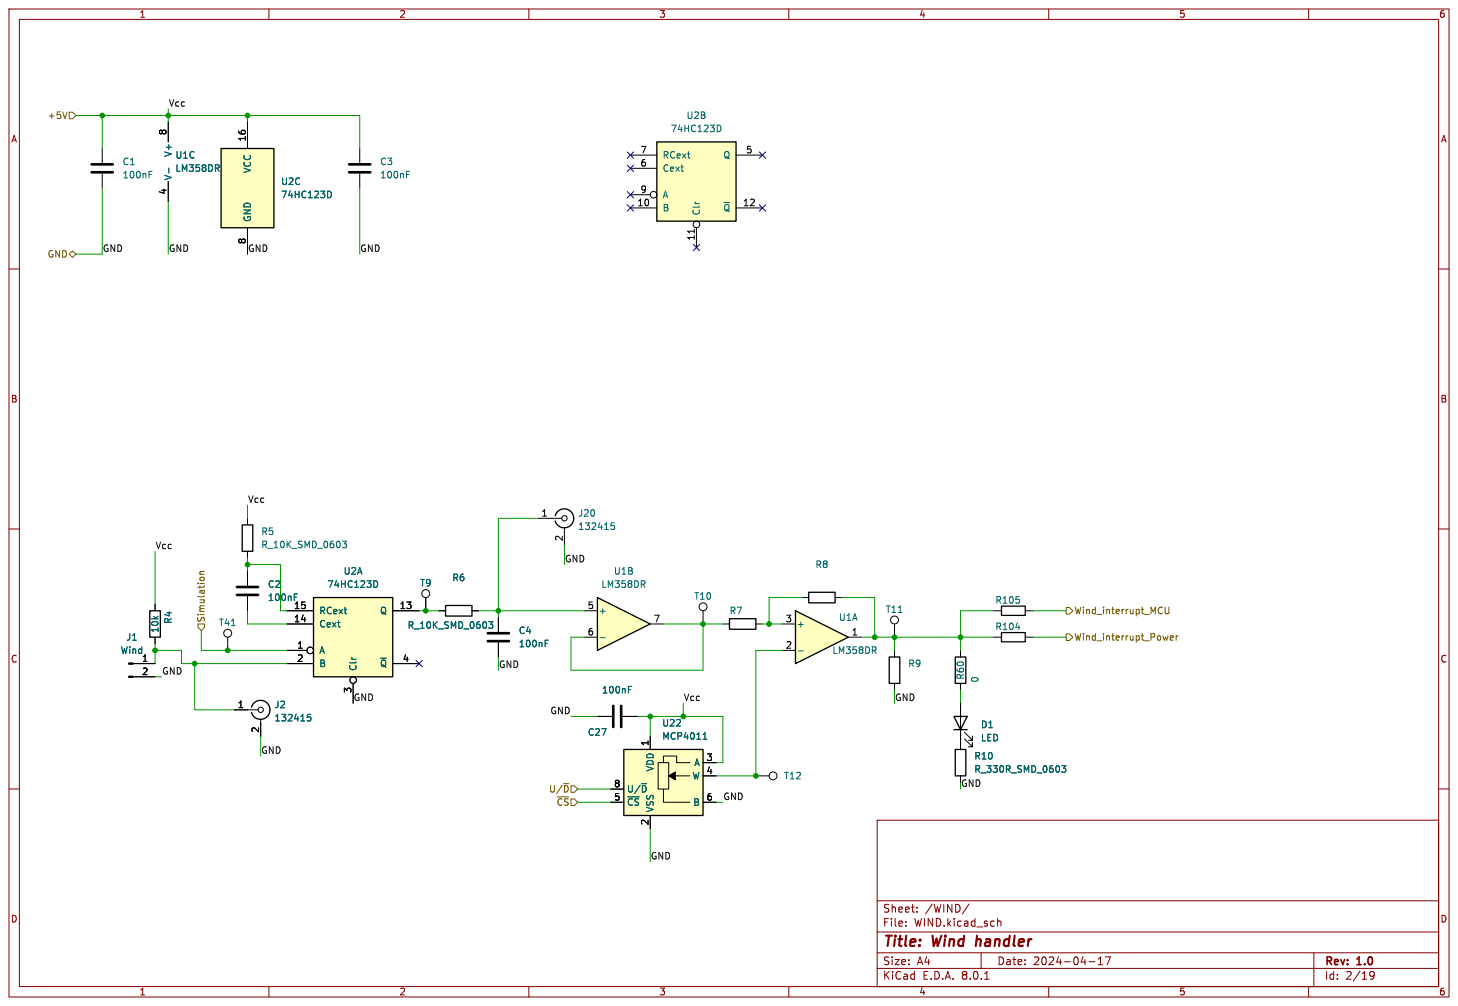
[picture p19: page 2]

Id: 2/19 Title: Wind handler File: WIND.kicad_sch Sheet: /WIND/ R7 V- 4 V+
R6 R_10K_SMD_0603 T9 U1C

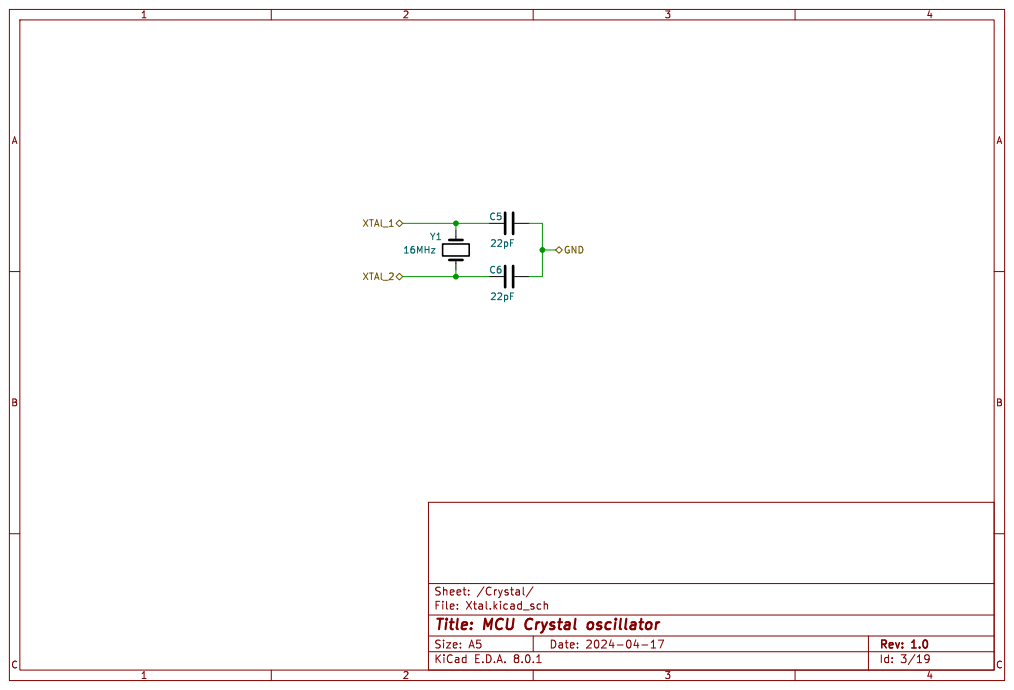
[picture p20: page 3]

Id: 3/19 Title: MCU Crystal oscillator File: Xtal.kicad_sch Sheet: /Crystal/ Y1

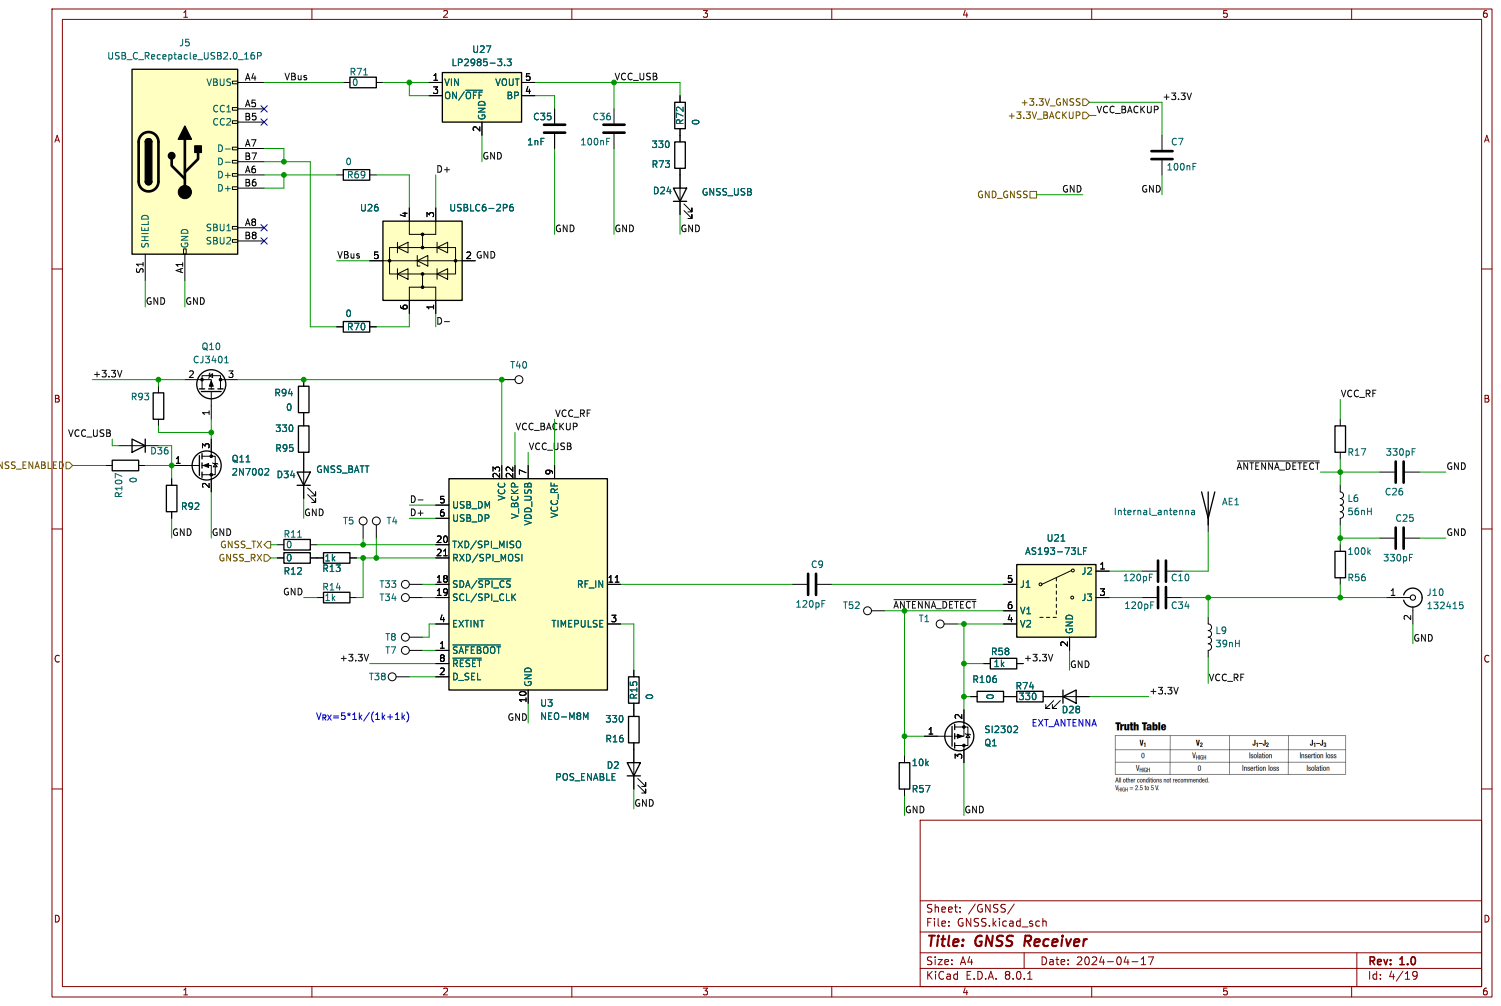
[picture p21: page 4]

2 ON/~{OFF} 3 BP 4 VOUT 5 U27
330 U3 NEO-M8M

2 ON/~{OFF} 3 BP 4 VOUT 5 R72

Id: 4/19 Title: GNSS Receiver File: GNSS.kicad_sch Sheet: /GNSS/ R72

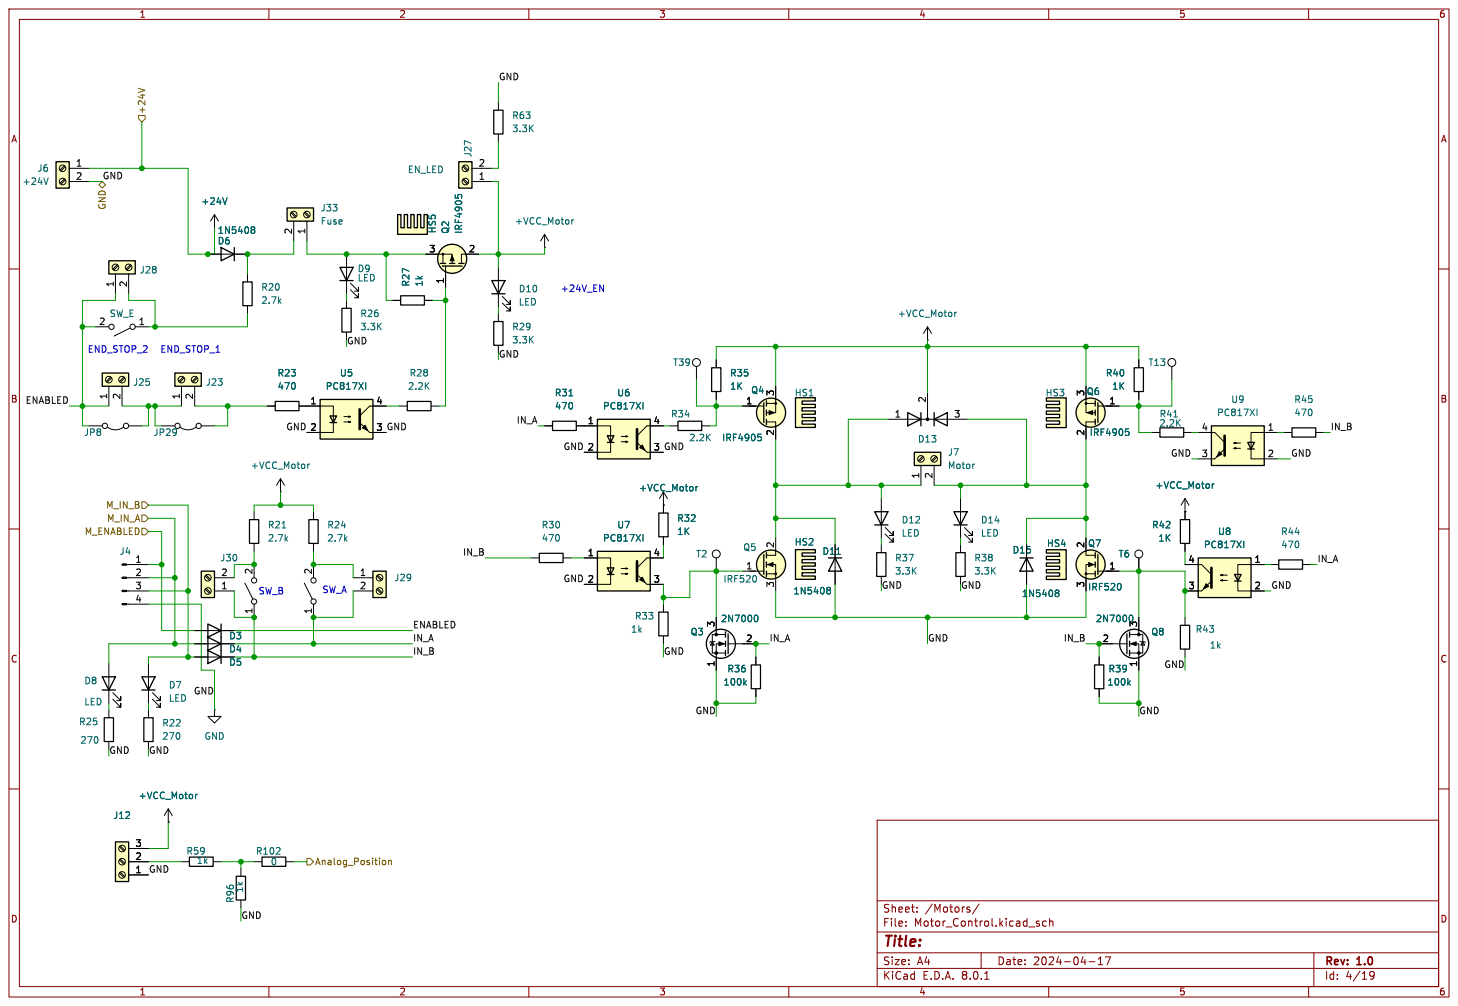
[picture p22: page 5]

Id: 4/19 Title: File: Motor_Control.kicad_sch Sheet: /Motors/ R30

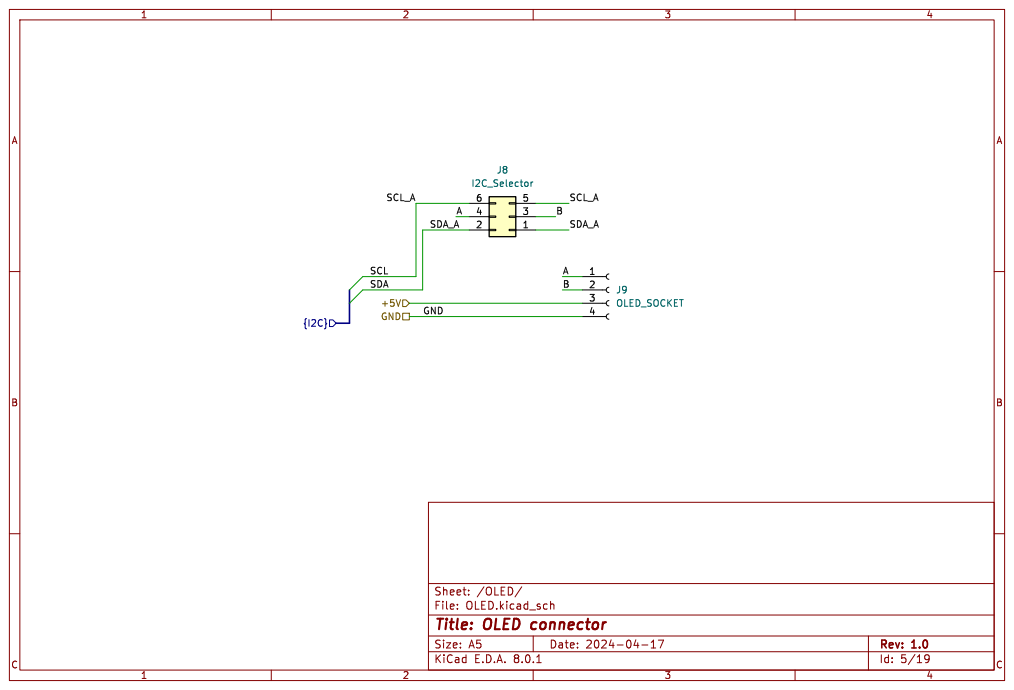
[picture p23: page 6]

Id: 5/19 Title: OLED connector File: OLED.kicad_sch Sheet: /OLED/

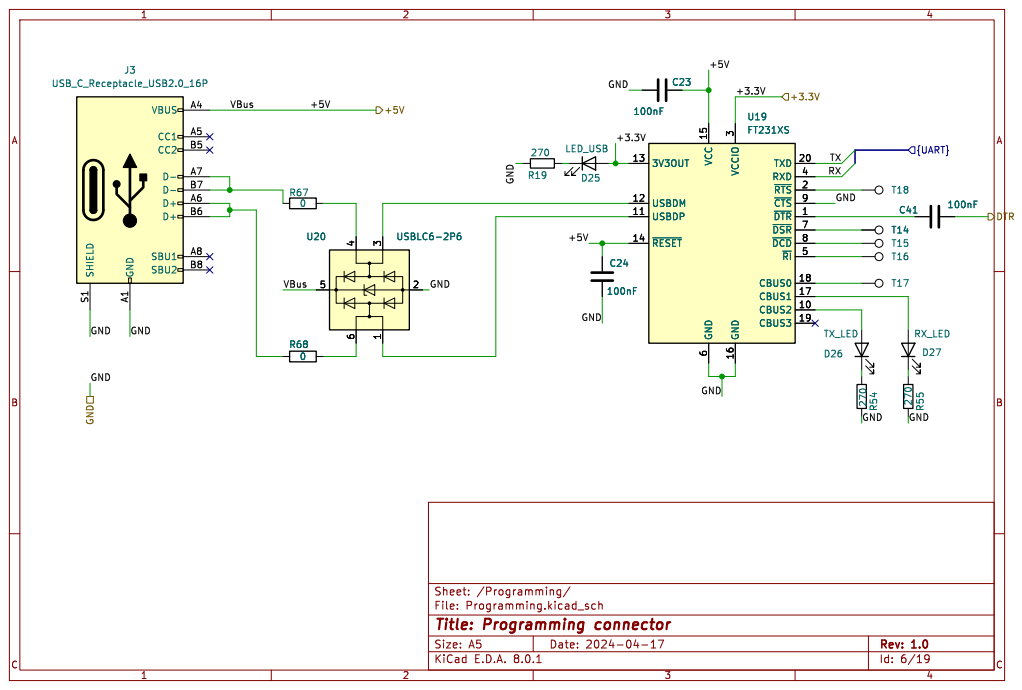
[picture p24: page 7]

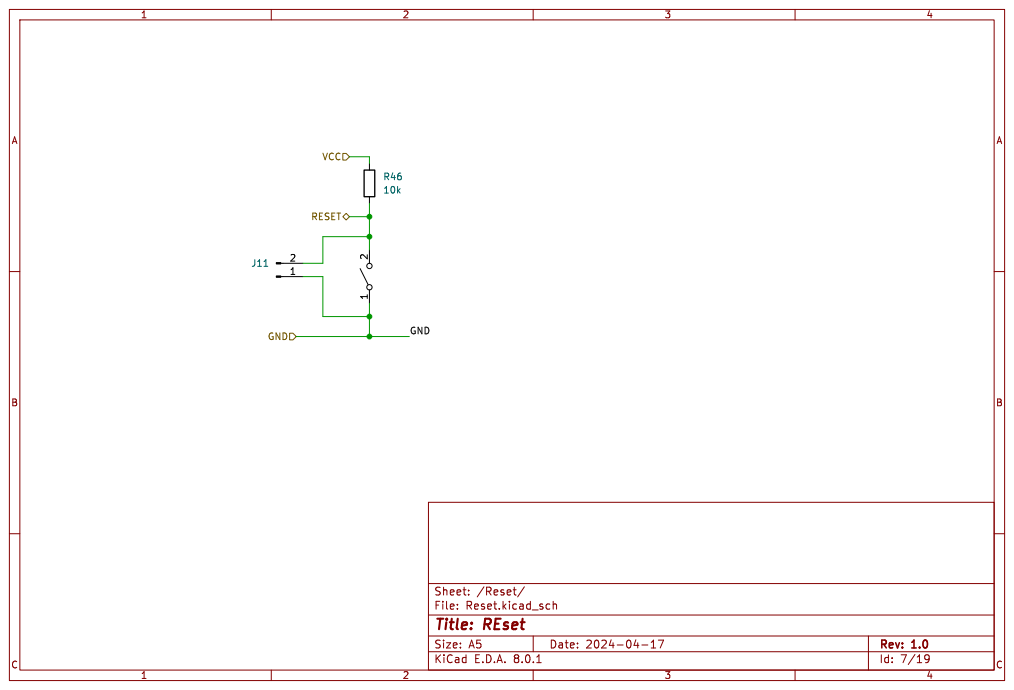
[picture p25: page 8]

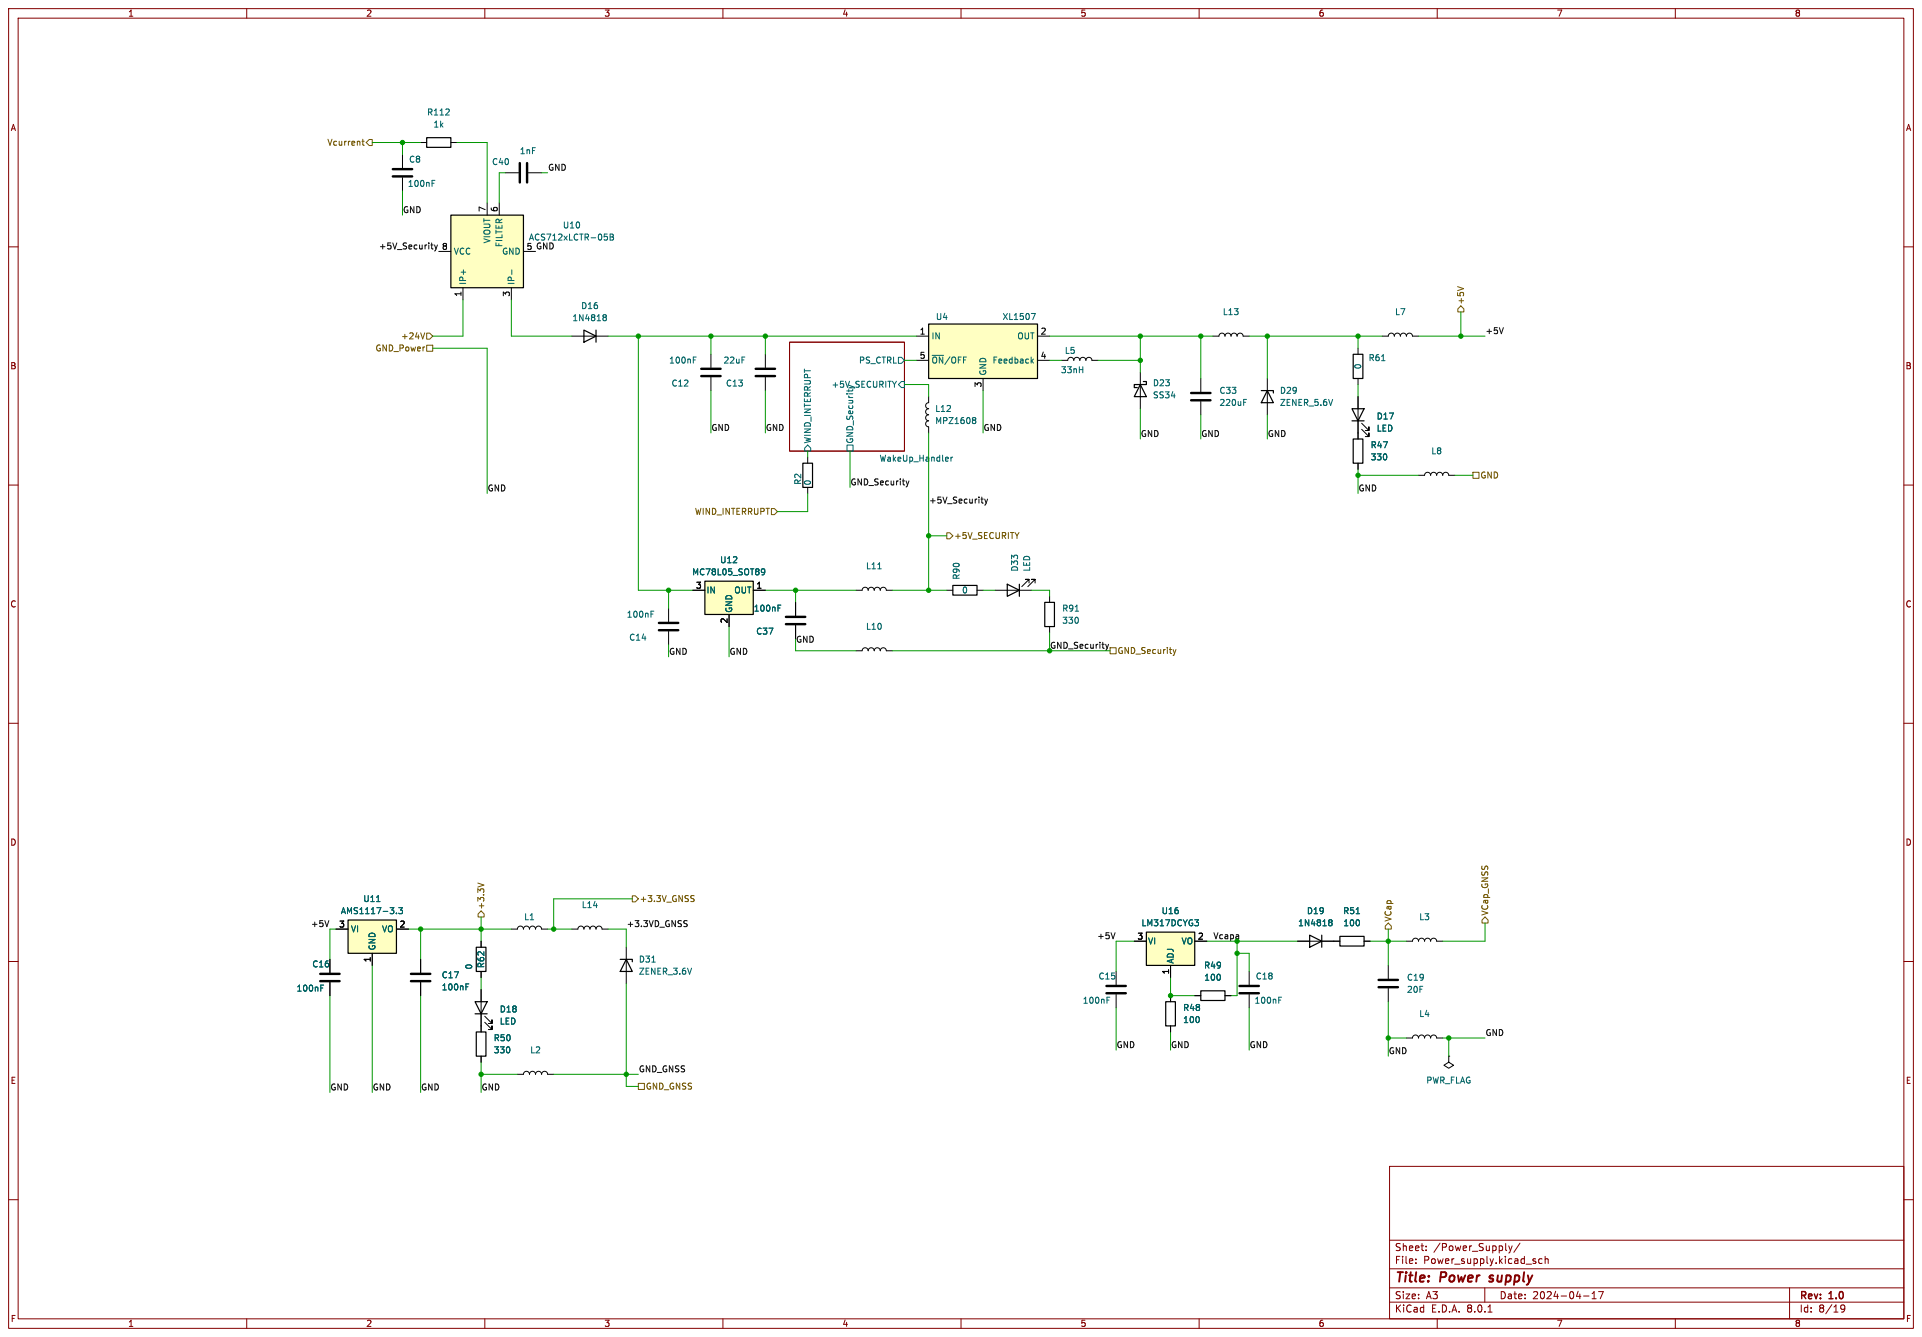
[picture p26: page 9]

Id: 8/19 Title: Power supply

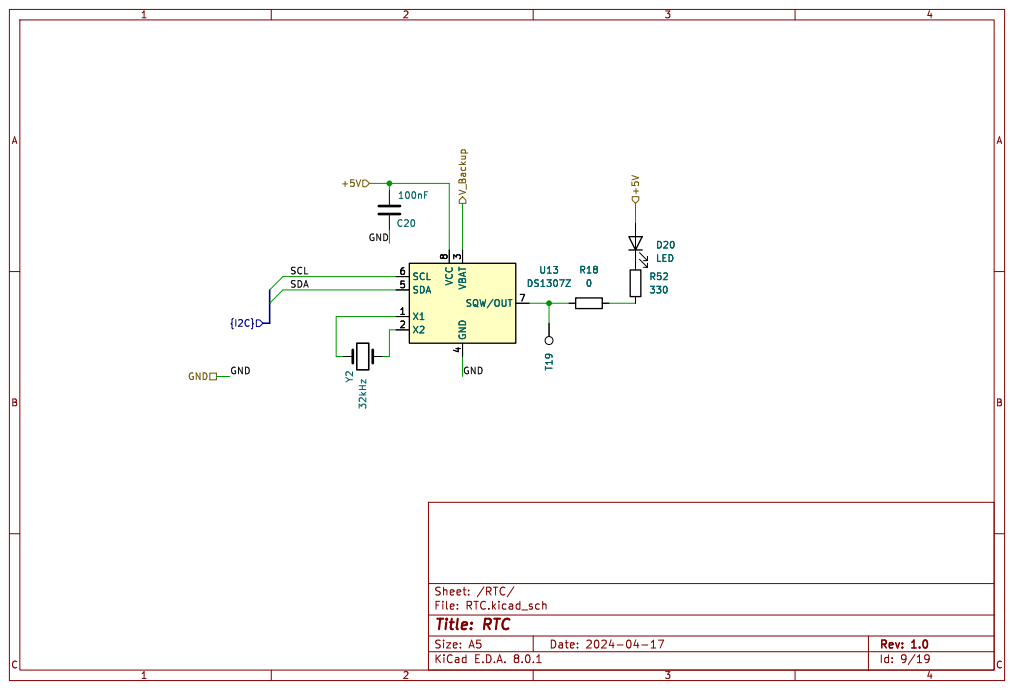
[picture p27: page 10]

4 SDA 5 SCL 6 SQW/OUT 7 VCC

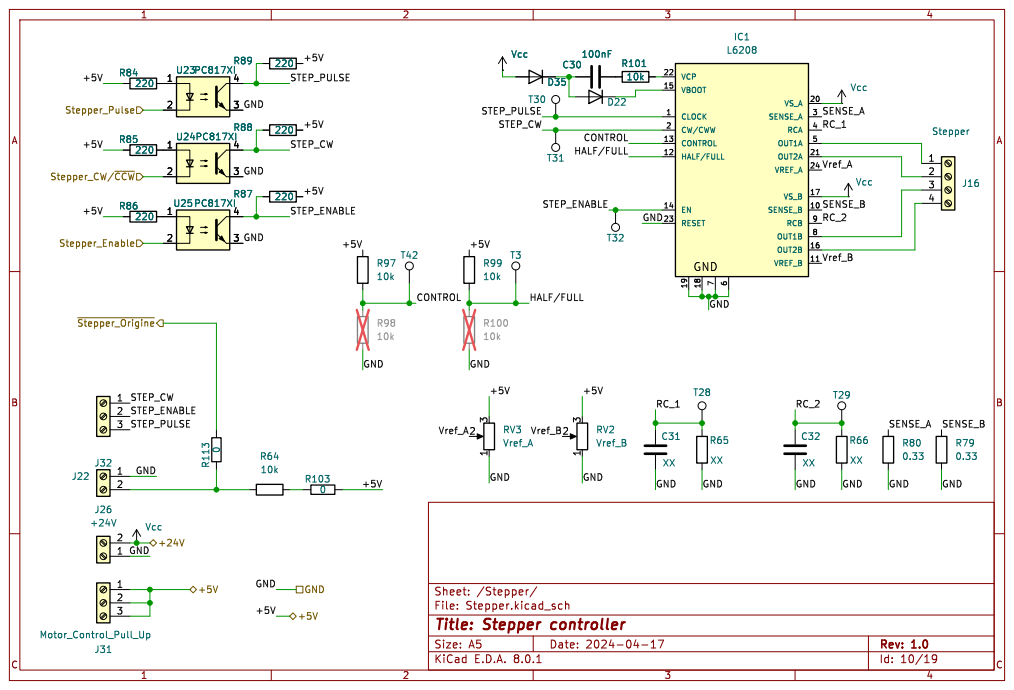
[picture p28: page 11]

Id: 10/19 Title: Stepper controller File: Stepper.kicad_sch Sheet: /Stepper/ T3

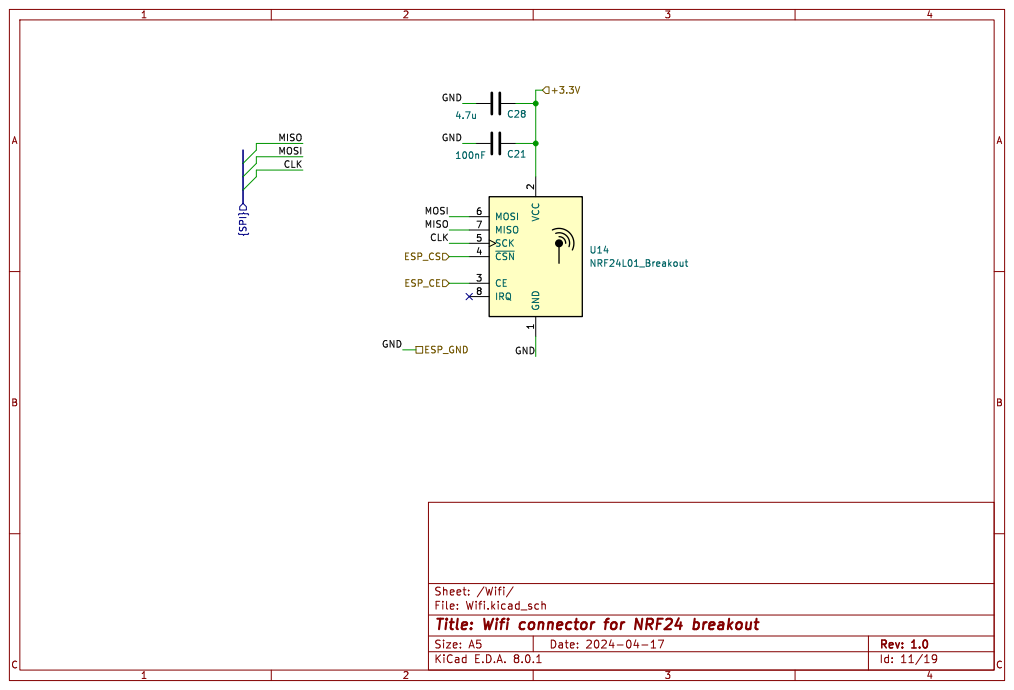
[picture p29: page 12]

2 CE 3 ~{CSN} 4 SCK 5 MOSI 6 MISO 7

Id: 11/19 Title: Wifi connector for NRF24 breakout File: Wifi.kicad_sch Sheet: /Wifi/


Id: 12/19 Title: Anemometer File: Anemometer.kicad_sch Sheet: /Anemometer/ T43 T45


Id: 13/19 Title: User actions


Id: 14/19 Title: MCU interfaces





Id: 19/19 Title: File: VoltageTranslator.kicad_sch Sheet: /SD_Reader/VoltageTranslator/

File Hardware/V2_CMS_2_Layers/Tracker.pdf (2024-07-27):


4 SDA 5 SCL 6 WP 7 VCC


Id: 2/18 Title: Wind handler File: WIND.kicad_sch Sheet: /WIND/ C27


Sheet: /Crystal/
File: Xtal.kicad_sch
Title: MCU Crystal oscillator


2 ON/~{OFF} 3 BP 4 VOUT 5 U27
VBus GND

2 ON/~{OFF} 3 BP 4 VOUT 5 C35

Id: 4/18 Title: GNSS Receiver File: GNSS.kicad_sch Sheet: /GNSS/ TP1


Id: 4/18 Title: File: Motor_Control.kicad_sch Sheet: /Motors/





Id: 8/18 Title: Power supply




Sheet: /Wifi/
File: Wifi.kicad_sch
Title: Wifi connector for NRF24 breakout










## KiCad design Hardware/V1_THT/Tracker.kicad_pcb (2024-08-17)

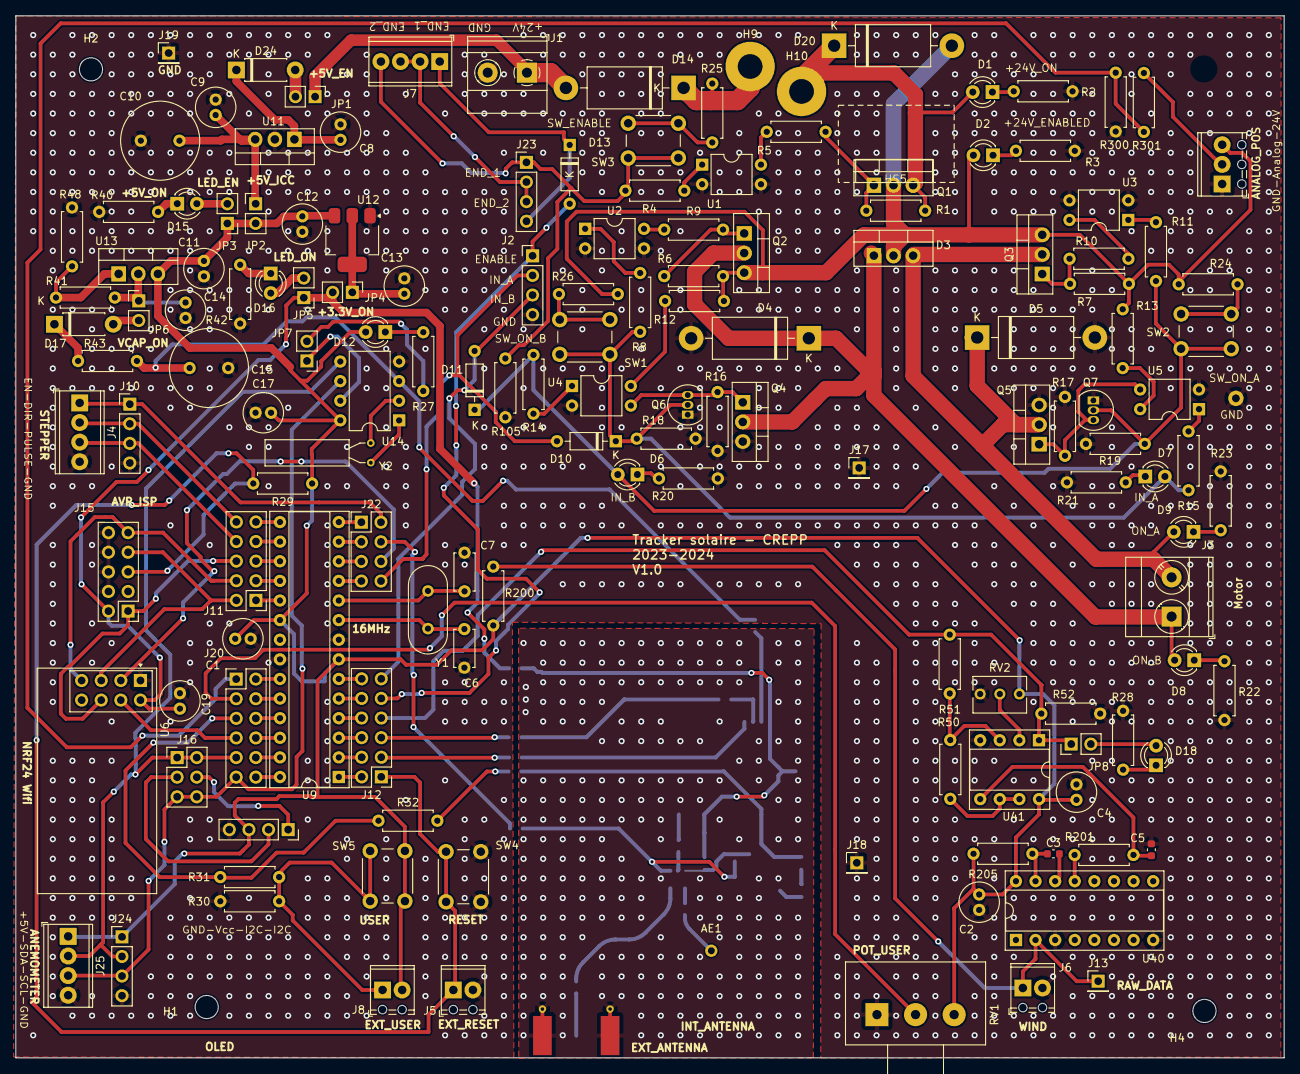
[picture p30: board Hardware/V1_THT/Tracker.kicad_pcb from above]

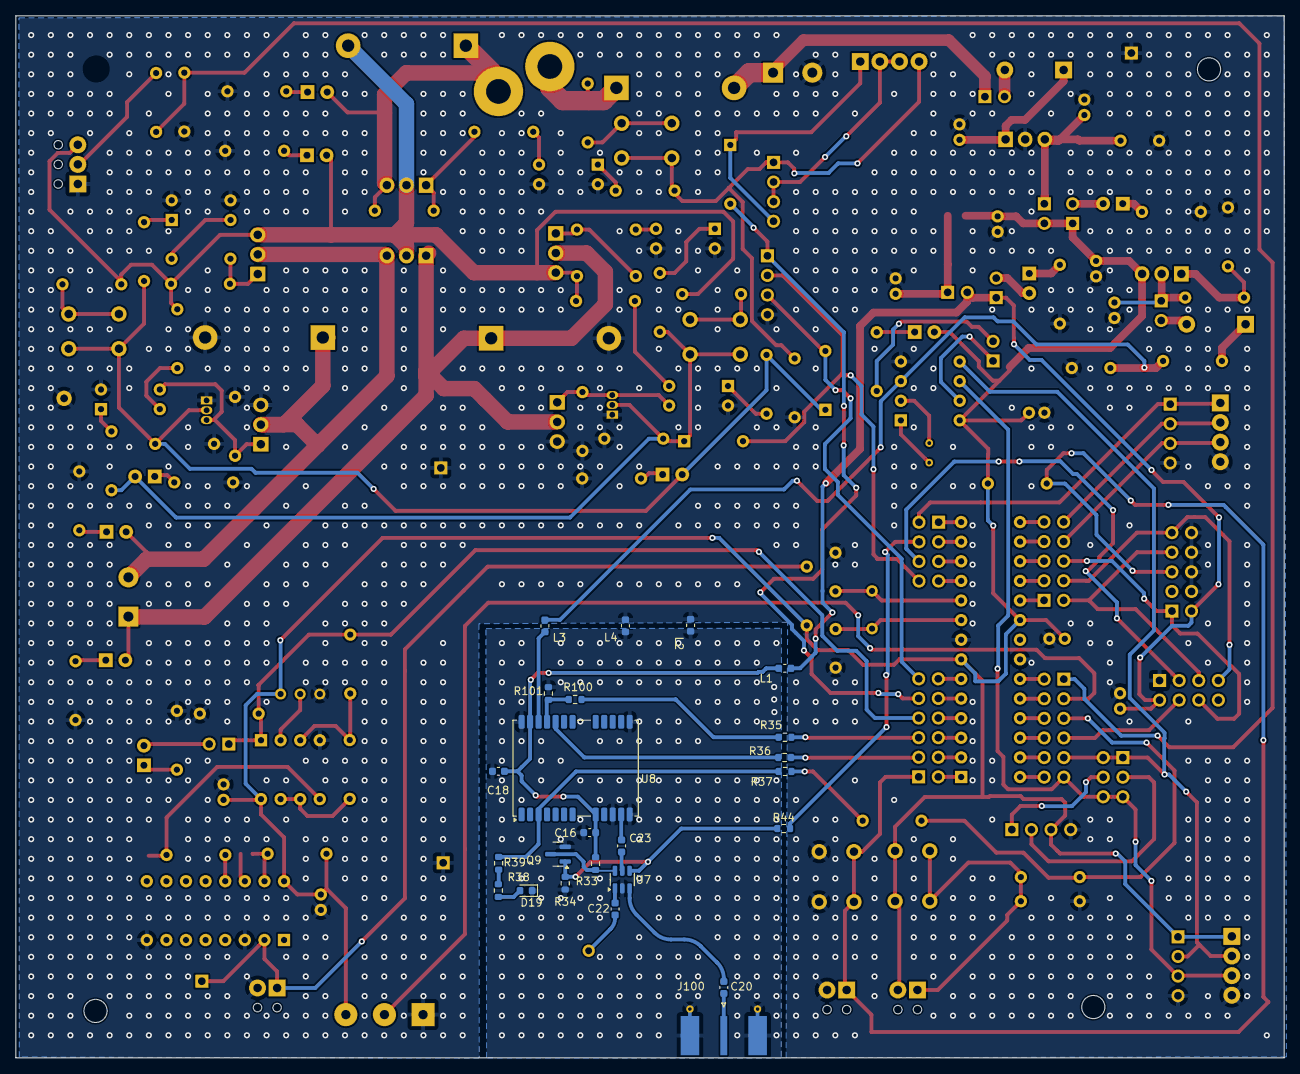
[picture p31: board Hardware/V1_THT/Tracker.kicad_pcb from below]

Board: 2 copper layers, 164.3 x 134.9 mm, 181 parts (24 on the bottom side), 132 nets.

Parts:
AE1: Internal_antenna; MountingHole_2.2mm_M2_DIN965_Pad
C1, C2, C4, C8, C9, C11, C12, C13, C14, C17, C19: 100nF; C_Radial_D5.0mm_H11.0mm_P2.00mm
C3, C5, C16, C18: 100nF; C_0603_1608Metric
C6, C7: 22pF; C_Disc_D4.7mm_W2.5mm_P5.00mm
C10: 1mF; C_Radial_D10.0mm_H16.0mm_P5.00mm
C15: 20F; C_Radial_D10.0mm_H20.0mm_P5.00mm
C20, C22, C23: 100pF; C_0603_1608Metric
D1, D2, D6, D7, D8, D9, D12, D15, D16, D18: LED; LED_D3.0mm
D3: D_Dual_CommonCathode_AAK; TO-220-3_Vertical
D4, D5, D14, D20: 1N5408; D_DO-201AD_P15.24mm_Horizontal
D10, D11, D13: 1N4148; D_DO-35_SOD27_P7.62mm_Horizontal
D17, D24: 1N4818; D_DO-41_SOD81_P7.62mm_Horizontal
D19: LED; LED_0603_1608Metric
H1, H2, H3, H4: MountingHole; MountingHole_3mm
H8: Probe_GND; Hole_1mm_Scope
H9, H10: MountingHole_Pad; MountingHole_3.2mm_M3_Pad
HS1, HS2, HS3, HS4, HS5: Heatsink; HeastSink_MOSFET_15mm_10mm_20mm
J1: +24V; TerminalBlock_Phoenix_MKDS-1,5-2-5.08_1x02_P5.08mm_Horizont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
J2, J10, J24: PinHeader_Control; PinHeader_1x04_P2.54mm_Vertical
J3: Motor; TerminalBlock_Phoenix_MKDS-3-2-5.08_1x02_P5.08mm_Horizontal
J4: Stepper; TerminalBlock_Phoenix_MPT-0,5-4-2.54_1x04_P2.54mm_Horizontal
J5, J8: USR_BTN; TerminalBlock_Phoenix_MPT-0,5-2-2.54_1x02_P2.54mm_Horizontal
J6: Wind; TerminalBlock_Phoenix_MPT-0,5-2-2.54_1x02_P2.54mm_Horizontal
J7: END_STOP_1_2; TerminalBlock_Phoenix_MPT-0,5-4-2.54_1x04_P2.54mm_Horizontal
J9: Analog_Position; TerminalBlock_Phoenix_MPT-0,5-3-2.54_1x03_P2.54mm_Horizontal
J11: Conn_02x05_Odd_Even; PinHeader_2x05_P2.54mm_Vertical
J12, J20: Conn_02x06_Odd_Even; PinHeader_2x06_P2.54mm_Vertical
J13: RAW_data_Wind; PinHeader_1x01_P2.54mm_Vertical
J14: OLED_SOCKET; PinSocket_1x04_P2.54mm_Vertical
J15: SPI_Programming; PinHeader_2x05_P2.54mm_Vertical
J16: I2C_Selector; PinHeader_2x03_P2.54mm_Vertical
J17, J18, J19: GND; PinHeader_1x01_P2.54mm_Vertical
J22: Conn_02x04_Odd_Even; PinHeader_2x04_P2.54mm_Vertical
J23: END_STOP_header; PinHeader_1x04_P2.54mm_Vertical
J25: Anemometer; TerminalBlock_Phoenix_MPT-0,5-4-2.54_1x04_P2.54mm_Horizontal
J100: 132134; SMA_Molex_73251-1153_EdgeMount_Horizontal
JP1, JP2, JP3, JP4, JP5, JP6, JP7, JP8: Jumper; PinHeader_1x02_P2.54mm_Vertical
L1, L2, L3, L4: L; L_0603_1608Metric
Q1, Q2, Q3: IRF4905; TO-220-3_Vertical
Q4, Q5: IRF520; TO-220-3_Vertical
Q6, Q7: 2N7000; TO-92_Inline
Q9: SI2302; SOT-23
R1, R25, R30, R31: 1k; R_Axial_DIN0207_L6.3mm_D2.5mm_P7.62mm_Horizontal
R2, R3, R22, R23: 3.3K; R_Axial_DIN0207_L6.3mm_D2.5mm_P7.62mm_Horizontal
R4, R8, R11, R14, R15: 120; R_Axial_DIN0207_L6.3mm_D2.5mm_P7.62mm_Horizontal
R5, R9, R10: 2.2K; R_Axial_DIN0207_L6.3mm_D2.5mm_P7.62mm_Horizontal
R6, R7, R12, R13: 1K; R_Axial_DIN0207_L6.3mm_D2.5mm_P7.62mm_Horizontal
R16, R17, R18, R19: 100k; R_Axial_DIN0207_L6.3mm_D2.5mm_P7.62mm_Horizontal
R20, R21, R27, R28, R40, R42: 270; R_Axial_DIN0207_L6.3mm_D2.5mm_P7.62mm_Horizontal
R24, R26: 2.7k; R_Axial_DIN0207_L6.3mm_D2.5mm_P7.62mm_Horizontal
R29, R50, R51, R52, R105, R201, R205, R300, R301: 10k; R_Axial_DIN0207_L6.3mm_D2.5mm_P7.62mm_Horizontal
R32: 2.2k; R_Axial_DIN0207_L6.3mm_D2.5mm_P7.62mm_Horizontal
R33, R100, R101: 1k; R_0603_1608Metric
R34: 10k; R_0603_1608Metric
R35, R36, R37, R39, R44: 0; R_0603_1608Metric
R38: 330; R_0603_1608Metric
R41, R43, R48: 100; R_Axial_DIN0207_L6.3mm_D2.5mm_P7.62mm_Horizontal
R200: 470k; R_Axial_DIN0207_L6.3mm_D2.5mm_P7.62mm_Horizontal
RV1: R_Potentiometer; Potentiometer_Alps_RK163_Single_Horizontal
RV2: R_Potentiometer; Potentiometer_Bourns_3266Y_Vertical
SW1: SW_A; SW_PUSH_6mm_H8mm
SW2, SW4: SW_B; SW_PUSH_6mm_H8mm
SW3: SW_E; SW_PUSH_6mm_H8mm
SW5: SW_User; SW_PUSH_6mm_H8mm
U1, U2, U3, U4, U5: PC817; DIP-4_W7.62mm
U6: NRF24L01_Breakout; nRF24L01_Breakout
U7: AS193-73; SOT-23-6
U8: NEO-M8M; ublox_NEO
U9: ATmega328P-P; DIP-28_W7.62mm_Socket
U11: L7805; TO-220-3_Vertical
U12: AMS1117-3.3; SOT-223-3_TabPin2
U13: LM317_TO-220; TO-220-3_Vertical
U14: DS1307+; DIP-8_W7.62mm
U40: 74HC123; DIP-16_W7.62mm_Socket
U41: LM358; DIP-8_W7.62mm_Socket
Y1: 16MHz; Crystal_HC49-4H_Vertical
Y2: 16MHz; Crystal_AT310_D3.0mm_L10.0mm_Horizontal

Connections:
+3.3V: C19.1, J15.2, JP4.2 (B), JP5.1 (A), L1.1, U6.2 (VCC)
+3.3V_GNSS: C16.2, C18.2, L1.2, R33.2, U8.8 (~RESET), U8.23 (VCC)
+5V: C1.2, C2.1, C4.1, C11.1, C12.1, C17.2, D12.2 (A), J8.2, J14.3, J24.1, J25.1, JP2.2 (B), JP3.1 (A), R29.1, R200.1, R205.1, RV1.3, RV2.1, SW5.1 (A), U9.7 (VCC), U9.20 (AVCC), U12.3 (VI), U13.3 (VI), U14.8 (VCC), U40.16 (VCC), U41.8 (V+)
+24V: D14.2 (A), J1.1, JP1.1 (A)
+VCC_Motor: D2.2 (A), D3.2 (K), D20.2 (A), J9.3, Q1.2 (D), Q2.3 (S), Q3.3 (S), R6.1, R7.1, R12.1, R13.1, R24.1, R26.1
+VCap: C15.1, L3.1, R43.2, U14.3 (VBAT)
+VCap_GNSS: L3.2, U8.22 (V_BCKP)
/Anemometer/SCL: J16.5, J16.6, J20.11, J24.3, J25.3, U14.6 (SCL)
/Anemometer/SDA: J16.1, J16.2, J20.9, J24.2, J25.2, U14.5 (SDA)
/Crystal/XTAl_1: C6.2, U9.9 (XTAL1/PB6), Y1.2
/Crystal/XTAl_2: C7.2, U9.10 (XTAL2/PB7), Y1.1
/GNSS/RX: J12.3, R36.1
/GNSS/TX: J12.5, R35.1
/GNSS/~INTERNAL_ANTENNA: Q9.1 (G), R34.2, R44.1, U7.4 (V2)
/MCU/CLK: J11.2, J15.7, U6.5 (SCK)
/MCU/MISO: J11.4, J15.9, U6.7 (MISO)
/MCU/MOSI: J11.6, J15.1, U6.6 (MOSI)
/MCU/PB0: J22.1, U9.14 (PB0)
/MCU/PB0-D8: J4.1, J10.1, J22.2
/MCU/PB1-D9~: J4.2, J10.2, J11.10
/MCU/PB2-D10~: J4.3, J10.3, J11.8
/MCU/PC0-A0: J20.1, R300.2, R301.2
/MCU/PC1-A1: J20.3, RV1.2
/MCU/PC3-A3: J20.7, U6.4 (~CSN)
/MCU/PD2-D2-(INT0): J12.7, JP8.1 (A), R51.2, R52.2, U41.1
/MCU/PD3-D3-(INT1)~: D13.2 (A), J2.1, J12.9
/MCU/PD4-D4: D11.2 (A), J2.3, J12.11
/MCU/PD5-D5~: D10.2 (A), J2.2, J22.8
/MCU/PD6-D6~: J22.6, U6.3 (CE)
/MCU/PD7-D7: J22.4, R44.2
/Motors/ENABLE: D13.1 (K), J7.1, J23.4
/Motors/IN_A: D7.2 (A), D10.1 (K), Q6.2 (G), R8.1, R15.2, R18.1, SW1.1 (A)
/Motors/IN_B: D6.2 (A), D11.1 (K), Q7.2 (G), R11.2, R14.1, R19.1, SW2.1 (A)
/OLED/A: J14.1, J16.4
/OLED/B: J14.2, J16.3
/Power_Supply/Vcapa: C14.1, JP6.1 (A), R41.2, U13.2 (VO)
/RST: J5.1, J12.1, J15.5, R29.2, SW4.2 (B)
/TIMEPULSE: R32.2, R37.2
/UserActions/Button: J8.1, R30.1, R31.2, SW5.2 (B)
/V_{A_{2}}: J20.5, R31.1, R32.1
GND: C1.1, C2.2, C4.2, C5.2, C6.1, C7.1, C8.2, C9.2, C10.2, C11.2, C12.2, C13.2, C14.2, C15.2, C17.1, C19.2, D4.2 (A), D5.2 (A), H8.1, J1.2, J2.4, J4.4, J5.2, J6.2, J9.1, J10.4, J14.4, J15.4, J15.6, J15.8, J15.10, J17.1, J18.1, J19.1, J24.4, J25.4, L2.1, L4.1, Q4.3 (S), Q5.3 (S), Q6.1 (S), Q7.1 (S), R2.2, R3.2, R16.2, R17.2, R18.2, R19.2, R20.2, R21.2, R22.2, R23.2, R28.2, R30.2, R40.2, R42.2, R48.1, R52.1, R105.2, R300.1, RV1.1, RV2.3, SW4.1 (A), U1.2, U1.3, U2.2, U2.3, U3.2, U3.3, U4.2, U5.2, U6.1 (GND), U9.8 (GND), U9.22 (GND), U11.2 (GND), U12.1 (GND), U14.4 (GND), U40.3 (Clr), U40.8 (GND), U41.4 (V-)
GND_GNSS: C16.1, C18.1, D19.1 (K), J100.2 (Ext), L2.2, L4.2, Q9.2 (S), R34.1, R101.2, U7.2 (GND), U8.10 (GND), U8.12 (GND), U8.13 (GND), U8.24 (GND)
unnamed: AE1.1 (A), C22.1
unnamed: D1.2 (A), D20.1 (K), H10.1, Q1.3 (S), R1.2
unnamed: D1.1 (K), R2.1
unnamed: D2.1 (K), R3.1
unnamed: D3.1 (A), D4.1 (K), D8.2 (A), J3.1, Q2.2 (D), Q4.2 (D)
unnamed: D3.3 (A), D5.1 (K), D9.2 (A), J3.2, Q3.2 (D), Q5.2 (D)
unnamed: D6.1 (K), R20.1
unnamed: D7.1 (K), R21.1
unnamed: D8.1 (K), R22.1
unnamed: D9.1 (K), R23.1
unnamed: D12.1 (K), R27.1
unnamed: D14.1 (K), H9.1, R25.1
unnamed: D15.2 (A), JP3.2 (B)
unnamed: D15.1 (K), R40.1
unnamed: D16.2 (A), JP5.2 (B)
unnamed: D16.1 (K), R42.1
unnamed: D17.2 (A), JP6.2 (B)
unnamed: D17.1 (K), R43.1
unnamed: D18.2 (A), JP8.2 (B)
unnamed: D18.1 (K), R28.1
unnamed: D19.2 (A), R38.1
unnamed: D24.2 (A), JP1.2 (B)
unnamed: C8.1, D24.1 (K), U11.1 (IN)
unnamed: J9.2, R301.1
unnamed: J11.1, U9.19 (PB5)
unnamed: J11.3, U9.18 (PB4)
unnamed: J11.5, U9.17 (PB3)
unnamed: J11.7, U9.16 (PB2)
unnamed: J11.9, U9.15 (PB1)
unnamed: J12.2, U9.1 (~RESET/PC6)
unnamed: J12.4, U9.2 (PD0)
unnamed: J12.6, U9.3 (PD1)
unnamed: J12.8, U9.4 (PD2)
unnamed: J12.10, U9.5 (PD3)
unnamed: J12.12, U9.6 (PD4)
unnamed: J6.1, J13.1, R200.2, U40.2 (B)
unnamed: J20.2, U9.23 (PC0)
unnamed: J20.4, U9.24 (PC1)
unnamed: J20.6, U9.25 (PC2)
unnamed: J20.8, U9.26 (PC3)
unnamed: J20.10, U9.27 (PC4)
unnamed: J20.12, U9.28 (PC5)
unnamed: J22.3, U9.13 (PD7)
unnamed: J22.5, U9.12 (PD6)
unnamed: J22.7, U9.11 (PD5)
unnamed: J7.4, J23.1, R4.1, R105.1, SW3.1 (A)
unnamed: J7.2, J7.3, J23.2, J23.3
unnamed: C20.1, J100.1 (In)
unnamed: C9.1, C10.1, JP2.1 (A), U11.3 (OUT)
unnamed: C13.1, JP4.1 (A), U12.2 (VO)
unnamed: JP7.1 (A), U14.7 (SQW/OUT)
unnamed: JP7.2 (B), R27.2
unnamed: Q1.1 (G), R1.1, R5.2
unnamed: Q2.1 (G), R6.2, R9.2
unnamed: Q3.1 (G), R7.2, R10.2
unnamed: Q4.1 (G), Q6.3 (D), R16.1, U4.3
unnamed: Q5.1 (G), Q7.3 (D), R17.1, U5.3
unnamed: Q9.3 (D), R33.1, U7.6 (V1)
unnamed: R4.2, U1.1
unnamed: R5.1, U1.4
unnamed: R8.2, U2.1
unnamed: R9.1, U2.4
unnamed: R10.1, U3.4
unnamed: R11.1, U3.1
unnamed: R12.2, U4.4
unnamed: R13.2, U5.4
unnamed: R14.2, U4.1
unnamed: R15.1, U5.1
unnamed: R38.2, R39.1
unnamed: R35.2, R100.1
unnamed: R26.2, SW1.2 (B)
unnamed: R24.2, SW2.2 (B)
unnamed: R25.2, SW3.2 (B)
unnamed: C22.2, U7.1 (RF1)
unnamed: C20.2, U7.3 (RF2)
unnamed: C23.1, U7.5 (RFC)
unnamed: C23.2, U8.11 (RF_IN)
unnamed: R100.2, R101.1, U8.21 (RXD/SPI_MOSI)
unnamed: R37.1, R39.2, U8.3 (TIMEPULSE)
unnamed: R36.2, U8.20 (TXD/SPI_MISO)
unnamed: R41.1, R48.2, U13.1 (ADJ)
unnamed: U14.1 (X1), Y2.2
unnamed: U14.2 (X2), Y2.1
unnamed: C3.2, U40.14 (Cext)
unnamed: R201.1, U40.13 (Q)
unnamed: C3.1, R205.2, U40.15 (RCext)
unnamed: R50.2, R51.1, U41.3 (+)
unnamed: RV2.2, U41.2 (-)
unnamed: C5.1, R201.2, U41.5 (+)
unnamed: R50.1, U41.6 (-), U41.7

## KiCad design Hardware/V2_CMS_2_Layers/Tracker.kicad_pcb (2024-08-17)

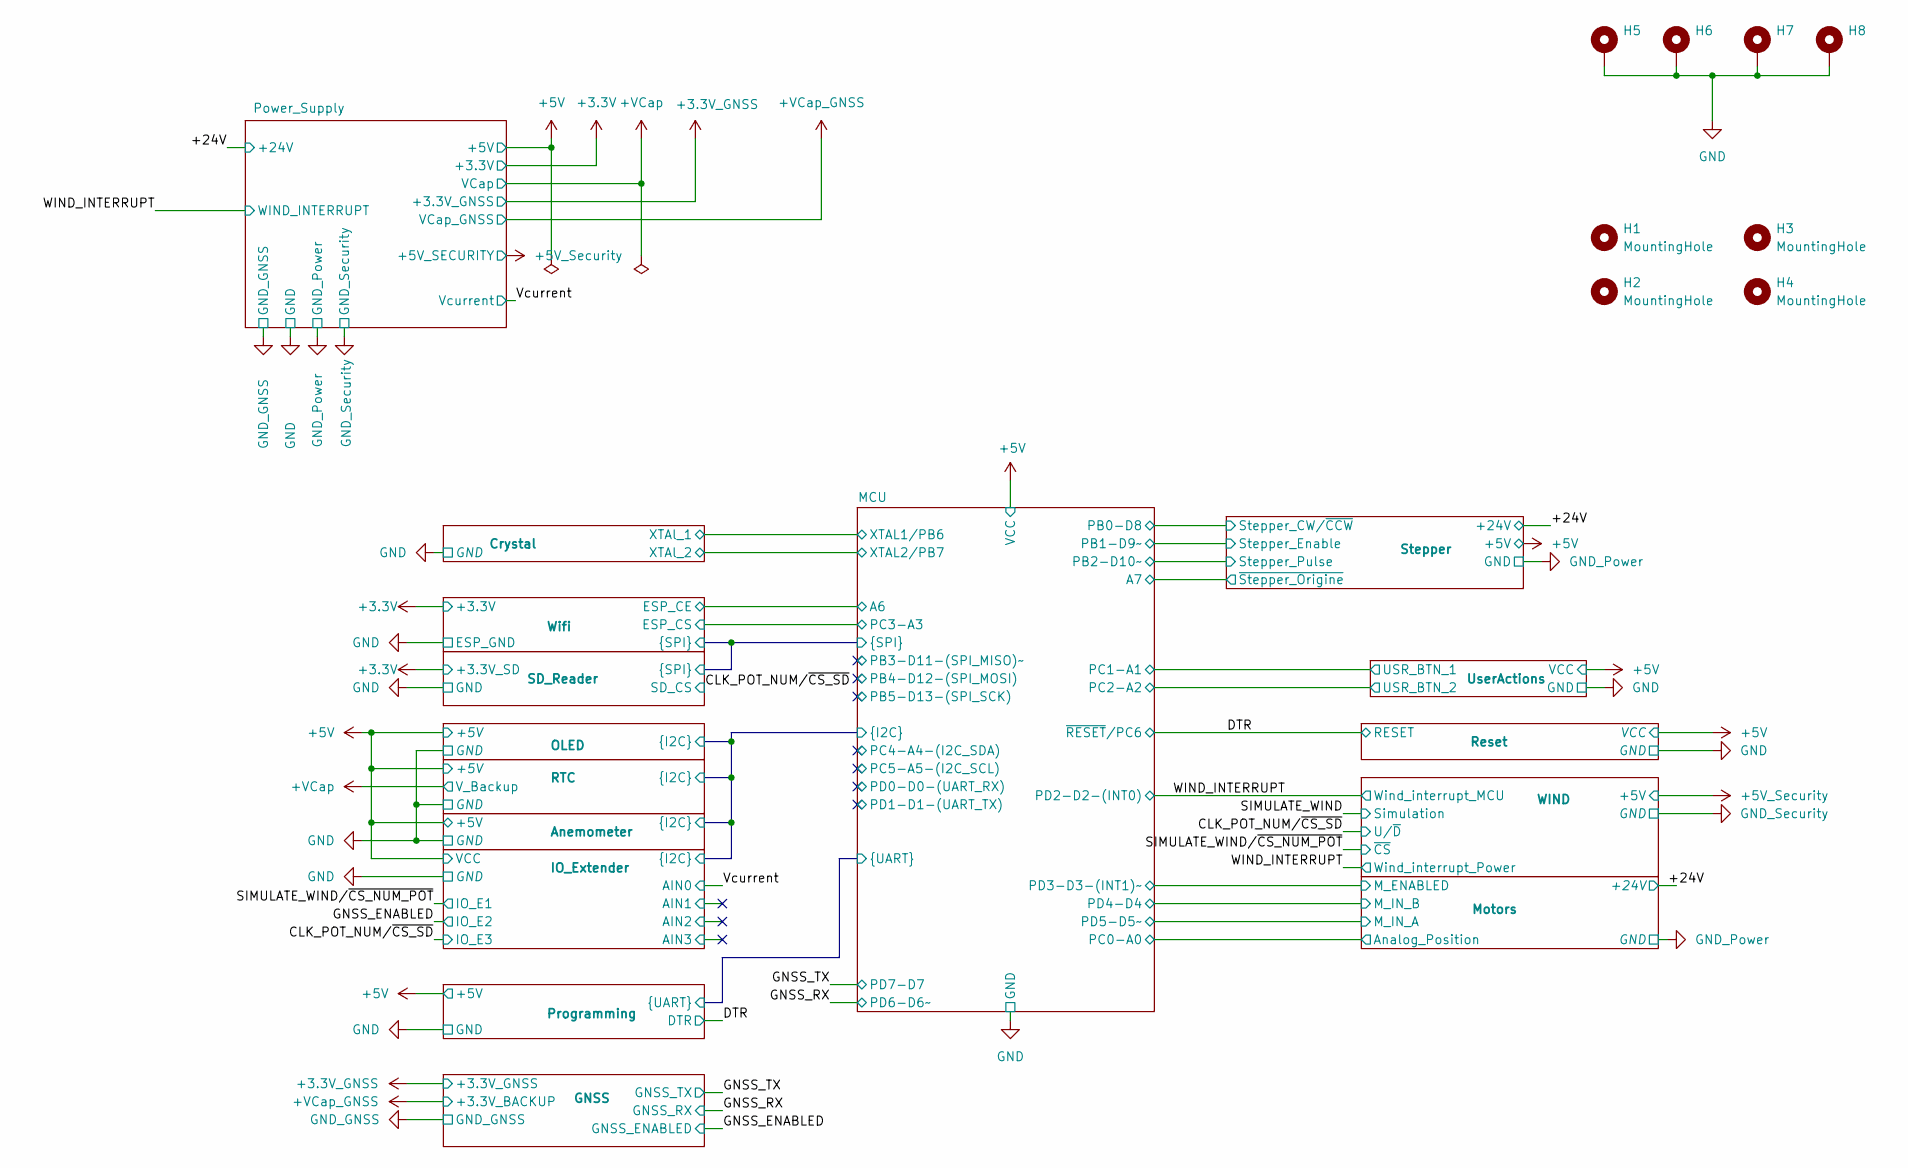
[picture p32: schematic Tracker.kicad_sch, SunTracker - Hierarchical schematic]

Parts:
H1, H2, H3, H4: MountingHole; MountingHole_3mm
H5, H6, H7, H8: Probe_GND; Hole_1mm_Scope

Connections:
unnamed: H5.1, H6.1, H7.1, H8.1

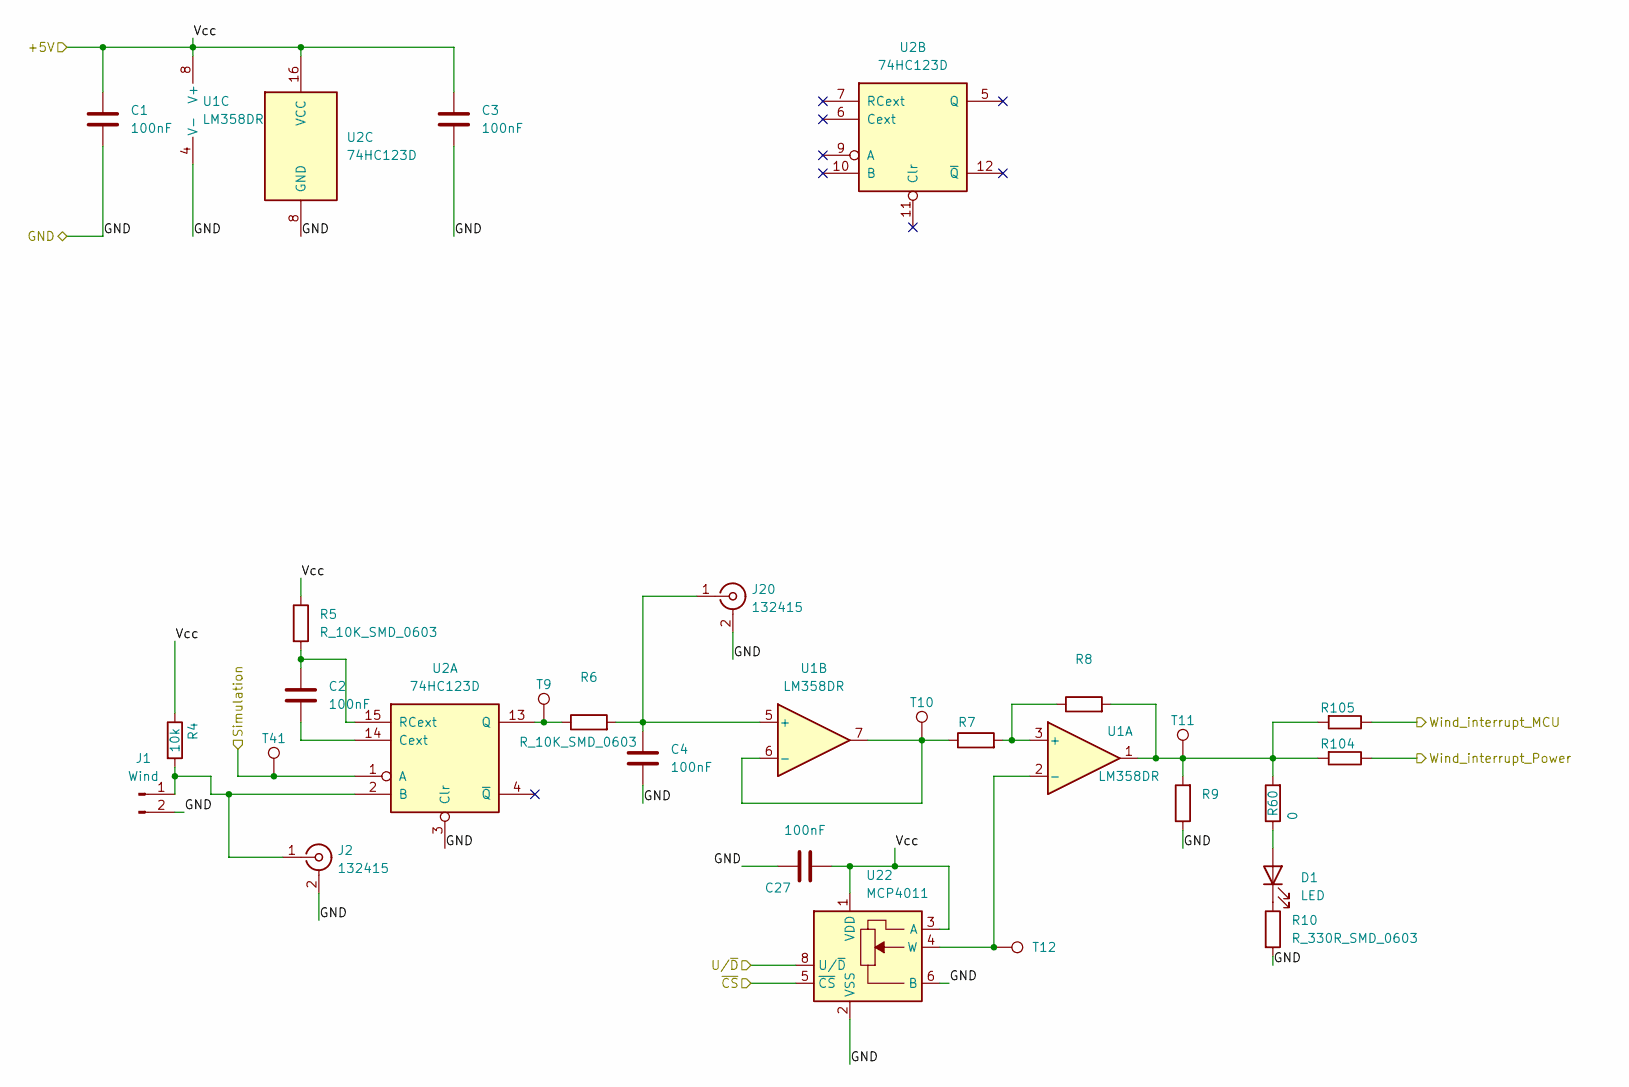
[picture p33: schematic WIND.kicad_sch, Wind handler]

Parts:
C1, C2, C3, C4, C27: 100nF; C_0603_1608Metric
D1: LED; LED_0603_1608Metric
J1: Wind; TerminalBlock_Phoenix_MPT-0,5-2-2.54_1x02_P2.54mm_Horizontal
J2, J20: 132415; SMA_Molex_73251-1153_EdgeMount_Horizontal
R4: 10k; R_0603_1608Metric
R5, R6, R7, R8, R9: R_10K_SMD_0603; R_0603_1608Metric
R10: R_330R_SMD_0603; R_0603_1608Metric
R60: 0; R_0603_1608Metric
R104, R105: R_0R_SMD_0603; R_0603_1608Metric
T9, T10, T11, T12, T41: TP; TestPoint_Pad_D1.0mm
U1: LM358DR; TSSOP-8_4.4x3mm_P0.65mm
U2: 74HC123D; SOIC-16W_5.3x10.2mm_P1.27mm
U22: MCP4011; SOIC-8_3.9x4.9mm_P1.27mm

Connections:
+5V_Security: C1.1, C3.1, C27.2, R4.1, R5.1, U1.8 (V+), U2.16 (VCC), U22.1 (VDD), U22.3 (A); also elsewhere on the board
/CLK_POT_NUM/~CS_SD: U22.8 (U/~D); also elsewhere on the board
/SIMULATE_WIND: T41.1, U2.1 (A)
/SIMULATE_WIND/~CS_NUM_POT: U22.5 (~CS); also elsewhere on the board
/WIND_INTERRUPT: R104.2, R105.2; also elsewhere on the board
GND_Security: C1.2, C3.2, C4.2, C27.1, J1.2, J2.2 (Ext), J20.2 (Ext), R9.1, R10.2, U1.4 (V-), U2.3 (Clr), U2.8 (GND), U22.2 (VSS), U22.6 (B); also elsewhere on the board
unnamed: D1.2 (A), R60.1
unnamed: D1.1 (K), R10.1
unnamed: J1.1, J2.1 (In), R4.2, U2.2 (B)
unnamed: C4.1, J20.1 (In), R6.2, U1.5 (+)
unnamed: R8.2, R9.2, R60.2, R104.1, R105.1, T11.1, U1.1
unnamed: R7.2, R8.1, U1.3 (+)
unnamed: T12.1, U1.2 (-), U22.4 (W)
unnamed: R7.1, T10.1, U1.6 (-), U1.7
unnamed: C2.2, U2.14 (Cext)
unnamed: R6.1, T9.1, U2.13 (Q)
unnamed: C2.1, R5.2, U2.15 (RCext)

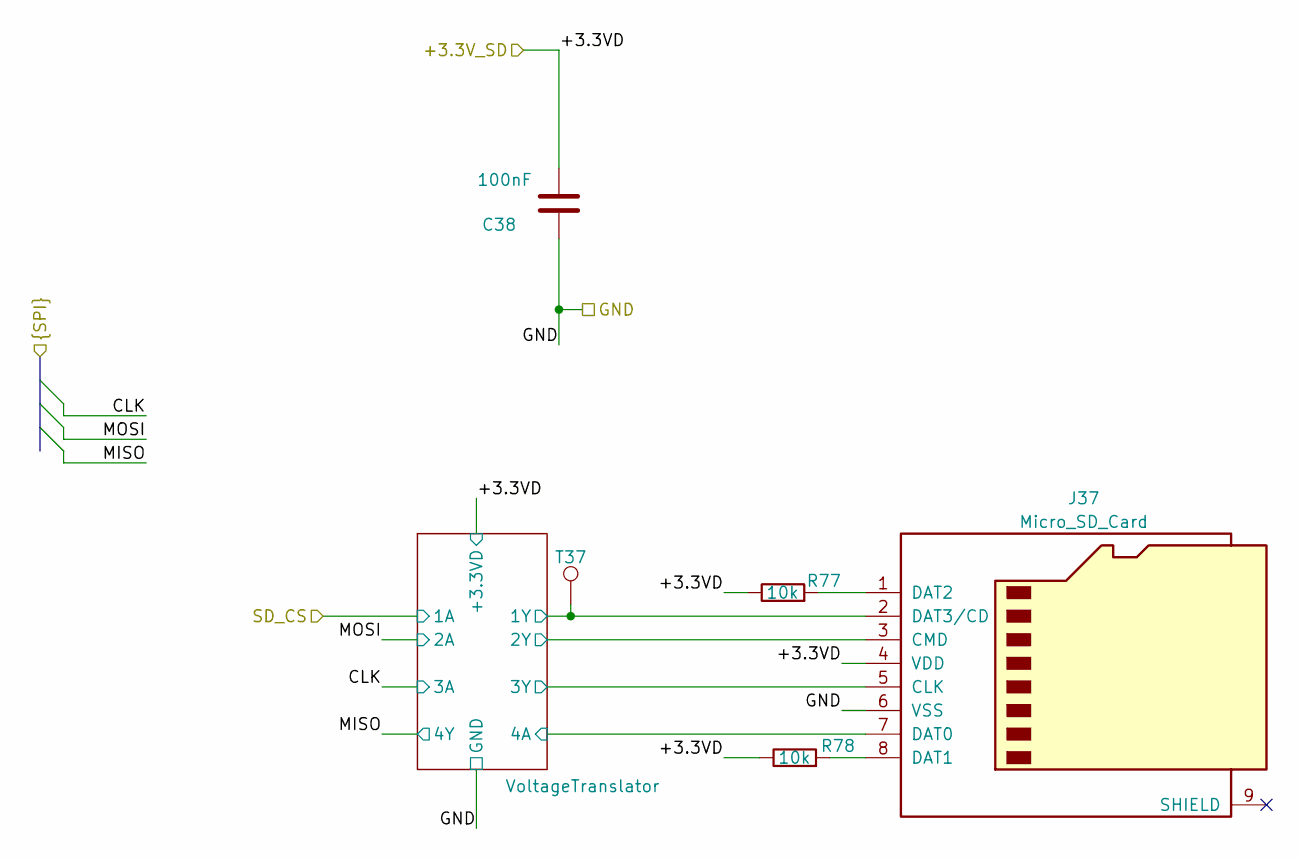
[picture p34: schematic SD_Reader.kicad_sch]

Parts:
C38: 100nF; C_0603_1608Metric
J37: Micro_SD_Card; microSD_HC_Hirose_DM3D-SF
R77, R78: 10k; R_0603_1608Metric
T37: TP; TestPoint_Pad_D1.0mm

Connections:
+3.3V: C38.1, J37.4 (VDD), R77.2, R78.2; also elsewhere on the board
/SD_Reader/VoltageTranslator/1Y: J37.2 (DAT3/CD), T37.1; also elsewhere on the board
/SD_Reader/VoltageTranslator/2Y: J37.3 (CMD); also elsewhere on the board
/SD_Reader/VoltageTranslator/3Y: J37.5 (CLK); also elsewhere on the board
/SD_Reader/VoltageTranslator/4A: J37.7 (DAT0); also elsewhere on the board
GND: C38.2, J37.6 (VSS); also elsewhere on the board
unnamed: J37.8 (DAT1), R78.1
unnamed: J37.1 (DAT2), R77.1

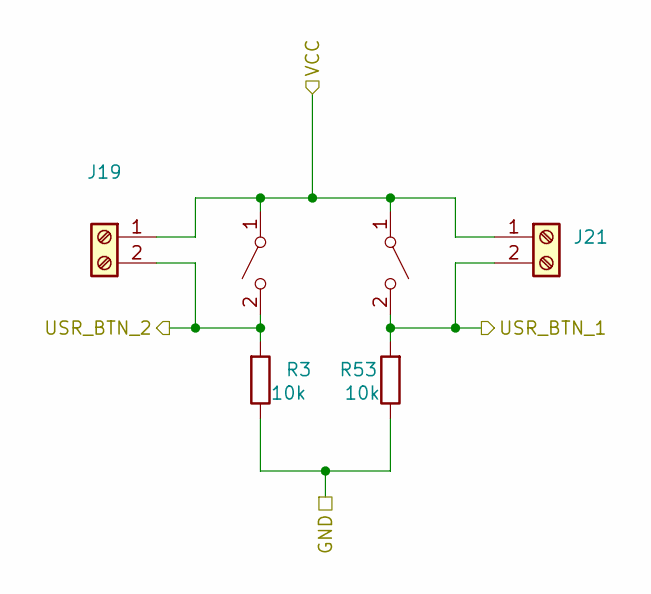
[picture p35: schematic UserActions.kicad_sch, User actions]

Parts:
J19, J21: KF128-2.54_2P; TerminalBlock_Phoenix_MPT-0,5-2-2.54_1x02_P2.54mm_Horizontal
R3, R53: 10k; R_0603_1608Metric
SW5, SW6: SW_User; SW_Push_1P1T_NO_CK_KSC7xxJ

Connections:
+5V: J19.1, J21.1, SW5.1 (A), SW6.1 (A); also elsewhere on the board
/MCU/PC1-A1: J21.2, R53.1, SW5.2 (B); also elsewhere on the board
/MCU/PC2-A2: J19.2, R3.1, SW6.2 (B); also elsewhere on the board
GND: R3.2, R53.2; also elsewhere on the board

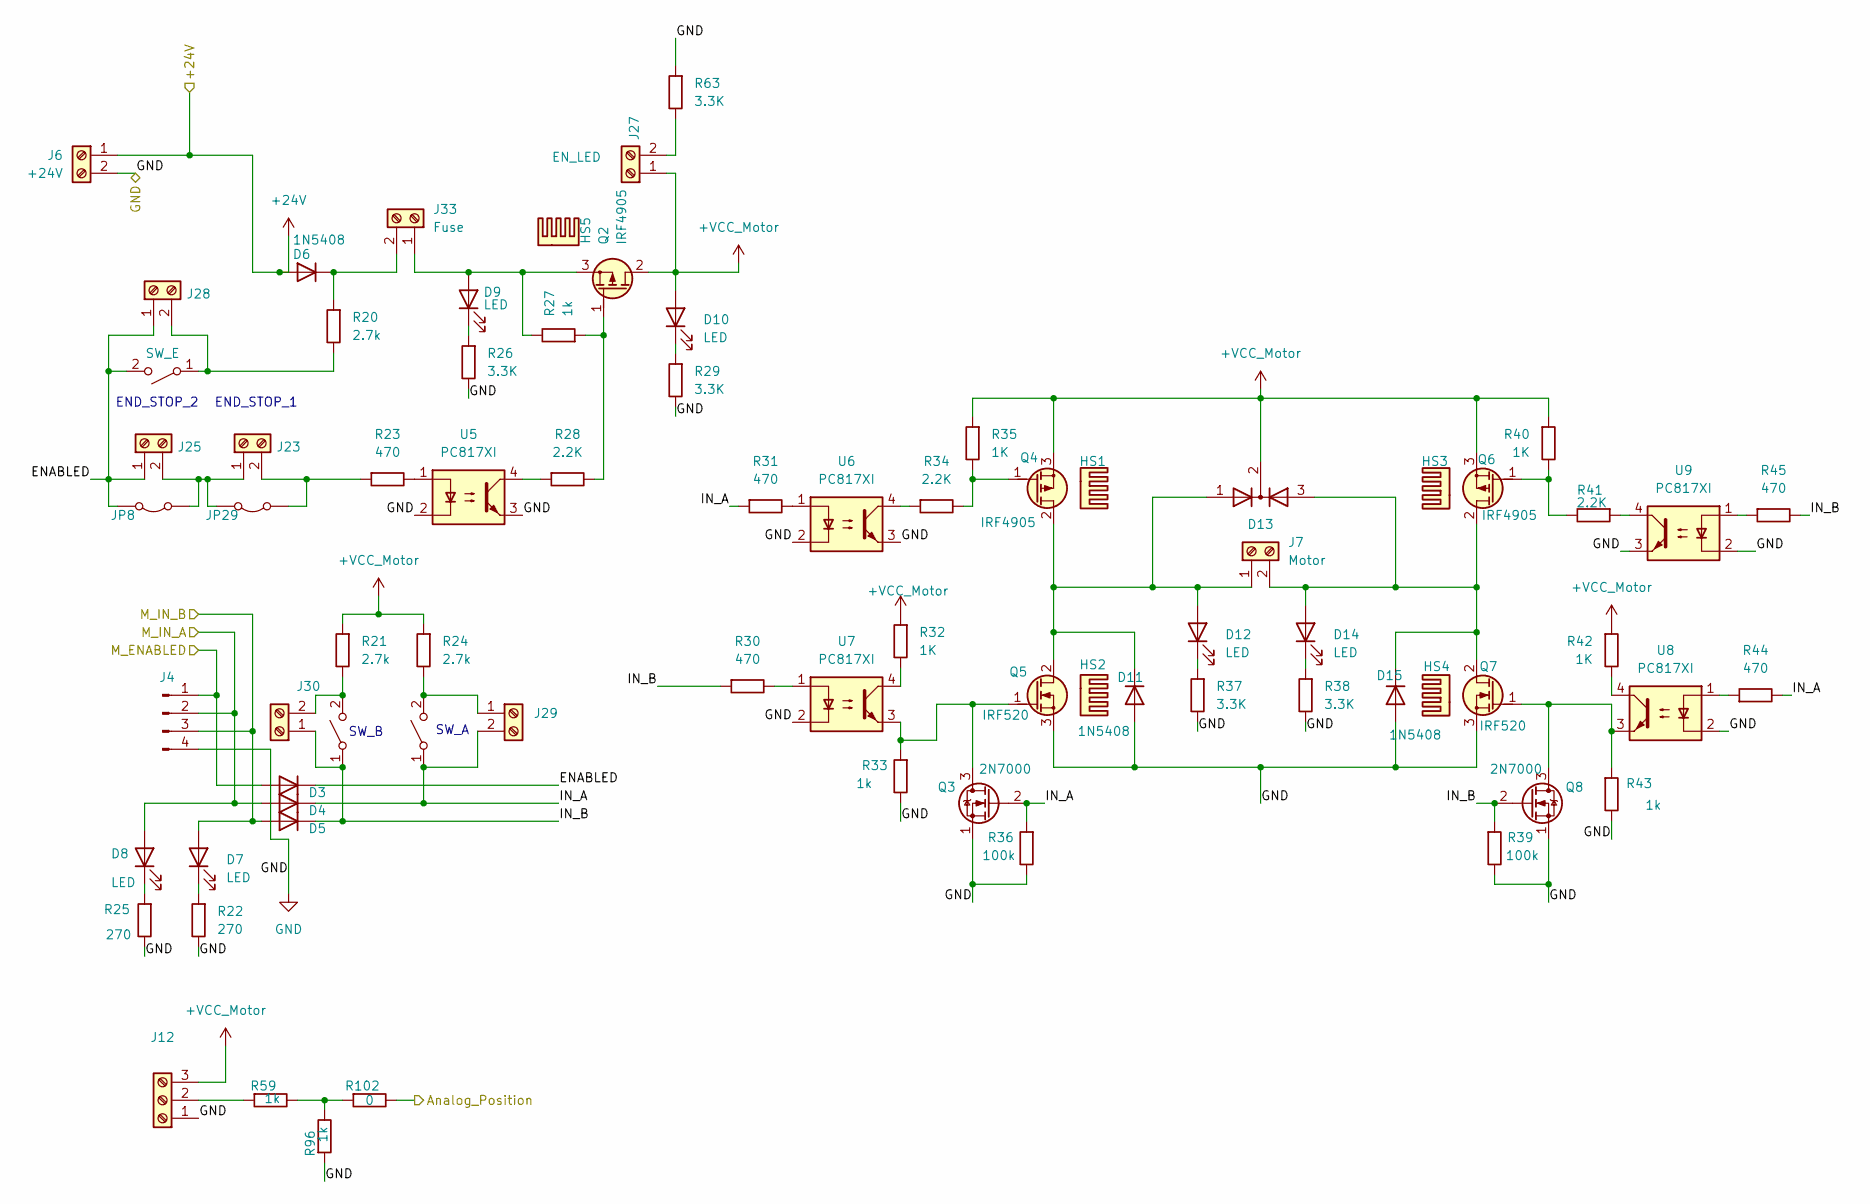
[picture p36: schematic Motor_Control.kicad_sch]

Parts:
D3, D4, D5: 1N4148; D_SOD-323
D6, D11, D15: 1N5408; D_DO-201AD_P15.24mm_Horizontal
D7, D8, D9, D10, D12, D14: LED; LED_0603_1608Metric
D13: D_Dual_CommonCathode_AAK; TO-220-3_Vertical
HS1, HS2, HS3, HS4, HS5: Heatsink; HeastSink_MOSFET_15mm_10mm_20mm
J4: PinHeader_Control; PinHeader_1x04_P2.54mm_Vertical
J6: +24V; PhoenixContact_MSTBA_2,5_2-G-5,08_1x02_P5.08mm_Horizontal
J7: Motor; PhoenixContact_MSTBA_2,5_2-G-5,08_1x02_P5.08mm_Horizontal
J12: KF128-2.54_3P; TerminalBlock_Phoenix_MPT-0,5-3-2.54_1x03_P2.54mm_Horizontal
J23, J25, J28, J29, J30: KF128-2.54_2P; TerminalBlock_Phoenix_MPT-0,5-2-2.54_1x02_P2.54mm_Horizontal
J27: EN_LED; TerminalBlock_Phoenix_MPT-0,5-2-2.54_1x02_P2.54mm_Horizontal
J33: Fuse; PhoenixContact_MSTBA_2,5_2-G-5,08_1x02_P5.08mm_Horizontal
JP8, JP29: Jumper; PinHeader_1x02_P2.54mm_Vertical
Q2, Q4, Q6: IRF4905; TO-220-3_Vertical
Q3, Q8: 2N7000; SOT-23-3
Q5, Q7: IRF520; TO-220-3_Vertical
R20, R21, R24: 2.7k; R_0603_1608Metric
R22, R25: 270; R_0603_1608Metric
R23, R30, R31, R44, R45: 470; R_0603_1608Metric
R26, R29, R37, R38, R63: 3.3K; R_0603_1608Metric
R27, R33, R43, R59, R96: 1k; R_0603_1608Metric
R28, R34, R41: 2.2K; R_0603_1608Metric
R32, R35, R40, R42: 1K; R_0603_1608Metric
R36, R39: 100k; R_0603_1608Metric
R102: 0; R_0603_1608Metric
SW1: SW_E; SW_Push_1P1T_NO_CK_KSC7xxJ
SW2, SW3: PB_SMD_12V_50MA_6MM_6MM; SW_Push_1P1T_NO_CK_KSC7xxJ
U5, U6, U7, U8, U9: PC817XI; SOP-4_4.4x2.6mm_P1.27mm

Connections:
+24V: D6.2 (A), J6.1; also elsewhere on the board
+VCC_Motor: D10.2 (A), D13.2 (K), J12.3, J27.1, Q2.2 (D), Q4.3 (S), Q6.3 (S), R21.1, R24.1, R32.1, R35.1, R40.1, R42.1
/MCU/PC0-A0: R102.2; also elsewhere on the board
/MCU/PD3-D3-(INT1)~: D3.2 (A), J4.1; also elsewhere on the board
/MCU/PD4-D4: D5.2 (A), D7.2 (A), J4.3; also elsewhere on the board
/MCU/PD5-D5~: D4.2 (A), D8.2 (A), J4.2; also elsewhere on the board
/Motors/ENABLED: D3.1 (K), J25.1, J28.1, JP8.2 (B), SW1.2 (B)
/Motors/IN_A: D4.1 (K), J29.2, Q3.2 (G), R31.1, R36.1, R44.2, SW3.1 (A)
/Motors/IN_B: D5.1 (K), J30.1, Q8.2 (G), R30.1, R39.1, R45.2, SW2.1 (A)
GND: D11.2 (A), D15.2 (A), J4.4, J6.2, J12.1, Q3.1 (S), Q5.3 (S), Q7.3 (S), Q8.1 (S), R22.2, R25.2, R26.2, R29.2, R33.2, R36.2, R37.2, R38.2, R39.2, R43.2, R63.1, R96.1, U5.2, U5.3, U6.2, U6.3, U7.2, U8.2, U9.2, U9.3; also elsewhere on the board
unnamed: D6.1 (K), J33.2, R20.1
unnamed: D7.1 (K), R22.1
unnamed: D8.1 (K), R25.1
unnamed: D9.2 (A), J33.1, Q2.3 (S), R27.2
unnamed: D9.1 (K), R26.1
unnamed: D10.1 (K), R29.1
unnamed: D11.1 (K), D12.2 (A), D13.1 (A), J7.1, Q4.2 (D), Q5.2 (D)
unnamed: D12.1 (K), R37.1
unnamed: D13.3 (A), D14.2 (A), D15.1 (K), J7.2, Q6.2 (D), Q7.2 (D)
unnamed: D14.1 (K), R38.1
unnamed: J12.2, R59.1
unnamed: J23.1, J25.2, JP8.1 (A), JP29.2 (B)
unnamed: J23.2, JP29.1 (A), R23.1
unnamed: J27.2, R63.2
unnamed: J28.2, R20.2, SW1.1 (A)
unnamed: J29.1, R24.2, SW3.2 (B)
unnamed: J30.2, R21.2, SW2.2 (B)
unnamed: Q2.1 (G), R27.1, R28.2
unnamed: Q3.3 (D), Q5.1 (G), R33.1, U7.3
unnamed: Q4.1 (G), R34.2, R35.2
unnamed: Q6.1 (G), R40.2, R41.2
unnamed: Q7.1 (G), Q8.3 (D), R43.1, U8.3
unnamed: R23.2, U5.1
unnamed: R28.1, U5.4
unnamed: R30.2, U7.1
unnamed: R31.2, U6.1
unnamed: R32.2, U7.4
unnamed: R34.1, U6.4
unnamed: R41.1, U9.4
unnamed: R42.2, U8.4
unnamed: R44.1, U8.1
unnamed: R45.1, U9.1
unnamed: R59.2, R96.2, R102.1

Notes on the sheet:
END_STOP_1
END_STOP_2
SW_B
SW_A

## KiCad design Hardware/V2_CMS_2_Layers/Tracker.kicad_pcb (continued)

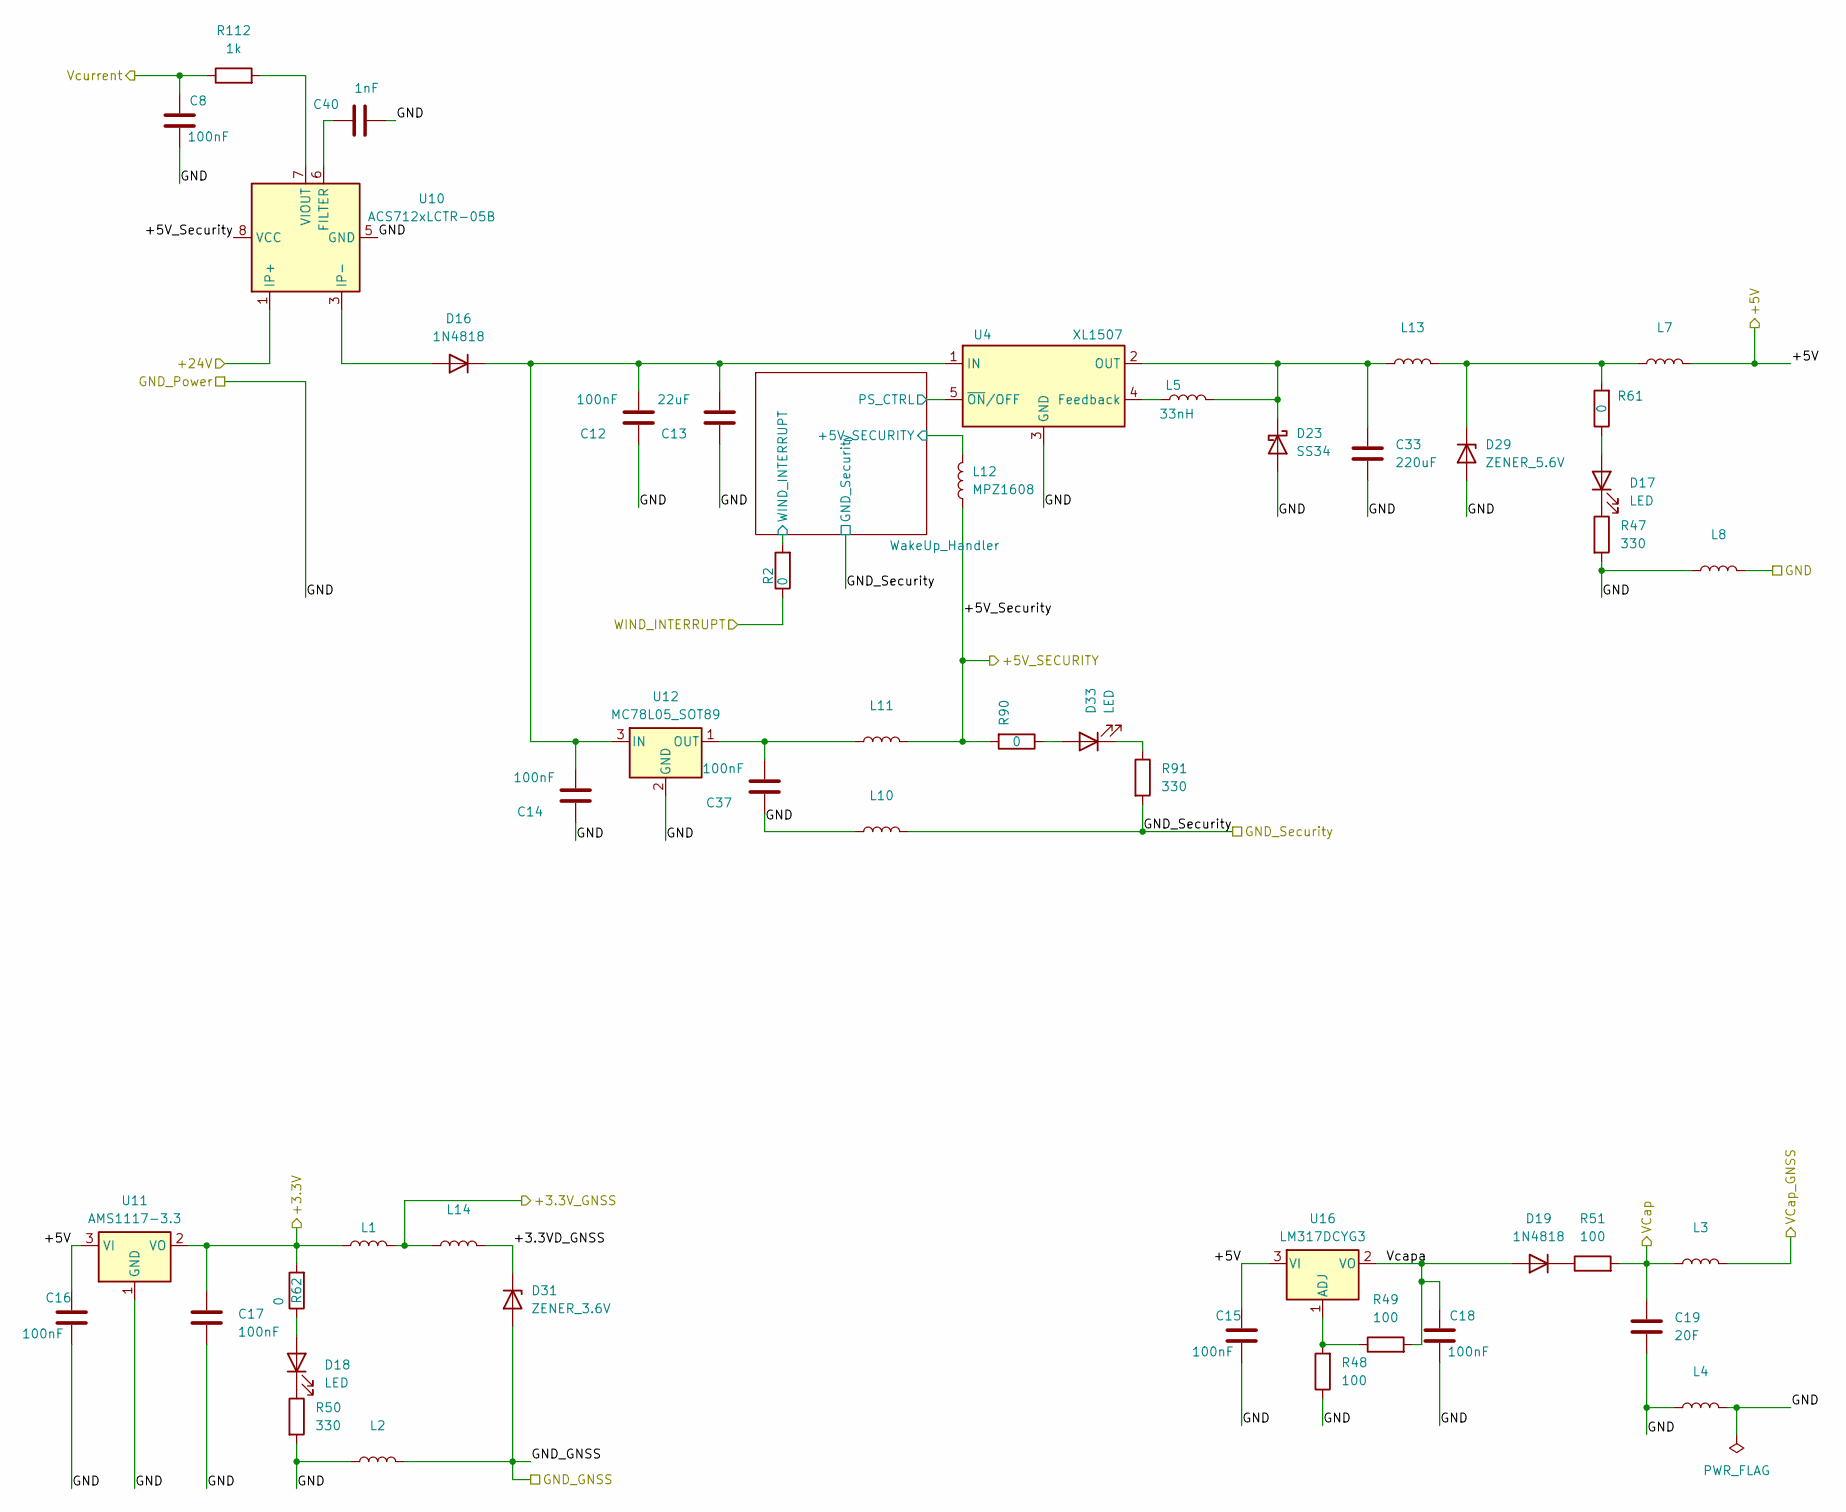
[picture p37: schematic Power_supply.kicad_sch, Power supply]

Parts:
C8, C12, C14, C15, C16, C17, C18, C37: 100nF; C_0603_1608Metric
C13: 22uF; C_0603_1608Metric
C19: 20F; C_Radial_D10.0mm_H20.0mm_P5.00mm
C33: 220uF; CP_Elec_6.3x7.7
C40: 1nF; C_0603_1608Metric
D16, D19: 1N4818; D_SOD-323
D17, D18, D33: LED; LED_0603_1608Metric
D23: SS34; D_SMA
D29: ZENER_5.6V; D_MiniMELF
D31: ZENER_3.6V; D_MiniMELF
L1, L2, L3, L4, L7, L8, L10, L11, L13, L14: MPZ1608S101ATAH0; L_0603_1608Metric
L5: 33nH; L_Wuerth_HCI-5040
L12: MPZ1608; L_0603_1608Metric
R2, R61, R62, R90: 0; R_0603_1608Metric
R47, R50, R91: 330; R_0603_1608Metric
R48, R49, R51: 100; R_0603_1608Metric
R112: 1k; R_0603_1608Metric
U4: XL1507; TO-252-5_TabPin3
U10: ACS712xLCTR-05B; SOIC-8_3.9x4.9mm_P1.27mm
U11: AMS1117-3.3; SOT-223-3_TabPin2
U12: MC78L05_SOT89; SOT-89-3
U16: LM317DCYG3; SOT-223-3_TabPin2

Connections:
+3.3V: C17.1, L1.1, R62.2, U11.2 (VO); also elsewhere on the board
+3.3V_GNSS: L1.2, L14.1; also elsewhere on the board
+5V: C15.1, C16.1, L7.2, U11.3 (VI), U16.3 (VI); also elsewhere on the board
+5V_Security: L11.2, L12.1, L12.2, R90.2, U10.8 (VCC); also elsewhere on the board
+24V: U10.1 (IP+), U10.2 (IP+); also elsewhere on the board
+VCap: C19.1, L3.1, R51.2; also elsewhere on the board
+VCap_GNSS: L3.2; also elsewhere on the board
/Power_Supply/+3.3VD_GNSS: D31.1 (K), L14.2
/Power_Supply/Vcapa: C18.1, D19.2 (A), R49.2, U16.2 (VO)
/Power_Supply/WakeUp_Handler/PS_CTRL: U4.5 (~ON/OFF); also elsewhere on the board
/Power_Supply/WakeUp_Handler/WIND_INTERRUPT: R2.2; also elsewhere on the board
/Vcurrent: C8.1, R112.1; also elsewhere on the board
/WIND_INTERRUPT: R2.1; also elsewhere on the board
GND: C8.2, C12.2, C13.2, C14.2, C15.2, C16.2, C17.2, C18.2, C19.2, C33.2, C37.2, C40.2, D23.2 (A), D29.2 (A), L2.1, L4.1, L4.2, L8.1, L8.2, L10.1, R47.2, R48.1, R50.2, U4.3 (GND), U10.5 (GND), U11.1 (GND), U12.2 (GND); also elsewhere on the board
GND_GNSS: D31.2 (A), L2.2; also elsewhere on the board
GND_Security: L10.2, R91.2; also elsewhere on the board
unnamed: D16.2 (A), U10.3 (IP-), U10.4 (IP-)
unnamed: C12.1, C13.1, C14.1, D16.1 (K), U4.1 (IN), U12.3 (IN)
unnamed: D17.2 (A), R61.1
unnamed: D17.1 (K), R47.1
unnamed: D18.2 (A), R62.1
unnamed: D18.1 (K), R50.1
unnamed: D19.1 (K), R51.1
unnamed: C33.1, D23.1 (K), L5.2, L13.1, U4.2 (OUT)
unnamed: D29.1 (K), L7.1, L13.2, R61.2
unnamed: D33.2 (A), R90.1
unnamed: D33.1 (K), R91.1
unnamed: L5.1, U4.4 (Feedback)
unnamed: C40.1, U10.6 (FILTER)
unnamed: R112.2, U10.7 (VIOUT)
unnamed: C37.1, L11.1, U12.1 (OUT)
unnamed: R48.2, R49.1, U16.1 (ADJ)

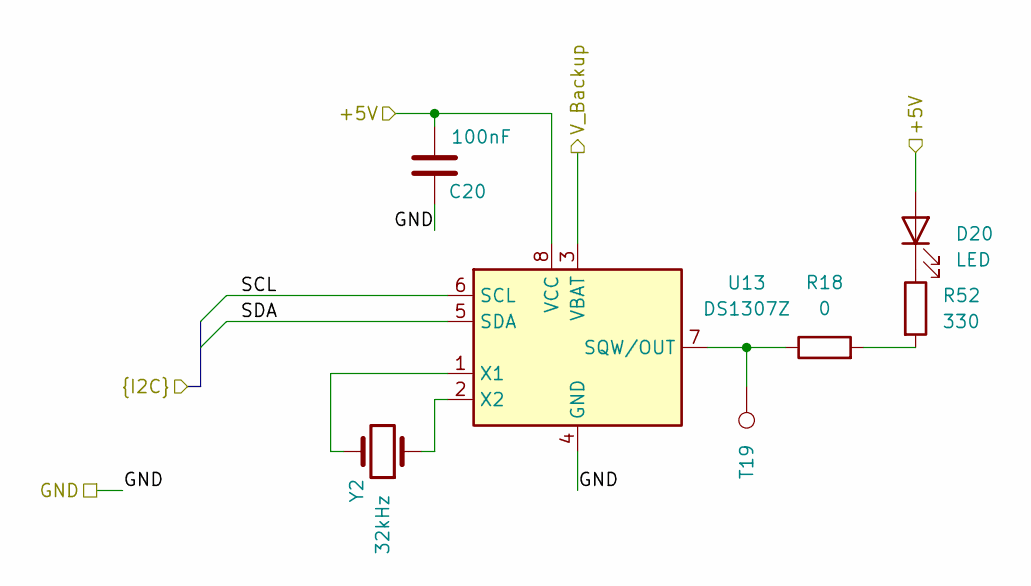
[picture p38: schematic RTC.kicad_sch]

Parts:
C20: 100nF; C_0603_1608Metric
D20: LED; LED_0603_1608Metric
R18: 0; R_0603_1608Metric
R52: 330; R_0603_1608Metric
T19: TP; TestPoint_Pad_D1.0mm
U13: DS1307Z; SO-8_5.3x6.2mm_P1.27mm
Y2: 32kHz; Crystal_SMD_3215-2Pin_3.2x1.5mm

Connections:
+5V: C20.1, D20.2 (A), U13.8 (VCC); also elsewhere on the board
+VCap: U13.3 (VBAT); also elsewhere on the board
/Anemometer/SCL: U13.6 (SCL); also elsewhere on the board
/Anemometer/SDA: U13.5 (SDA); also elsewhere on the board
GND: C20.2, U13.4 (GND); also elsewhere on the board
unnamed: D20.1 (K), R52.1
unnamed: R18.2, R52.2
unnamed: R18.1, T19.1, U13.7 (SQW/OUT)
unnamed: U13.1 (X1), Y2.2
unnamed: U13.2 (X2), Y2.1

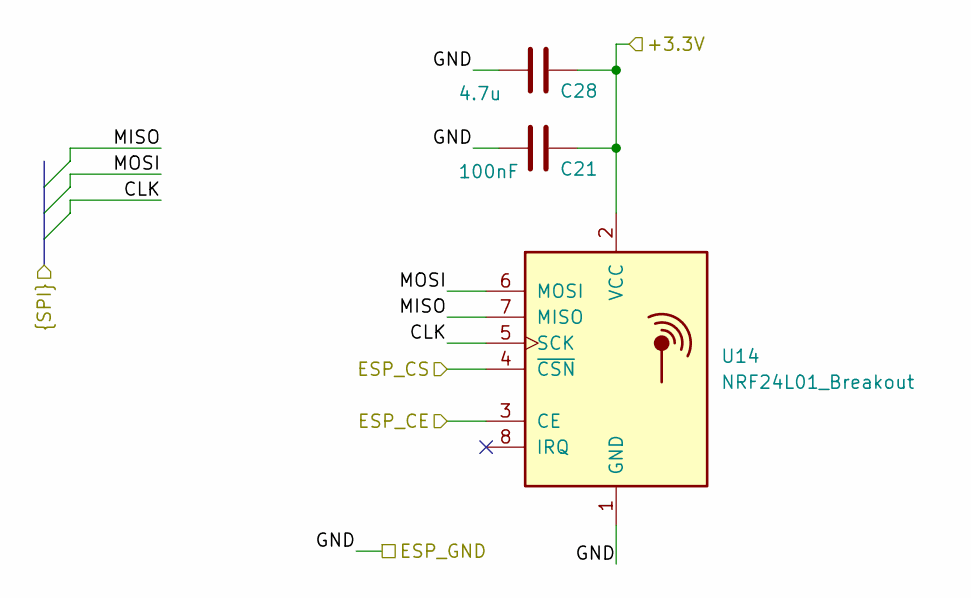
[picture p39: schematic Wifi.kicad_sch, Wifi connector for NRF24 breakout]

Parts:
C21: 100nF; C_0603_1608Metric
C28: 4.7u; C_0603_1608Metric
U14: NRF24L01_Breakout; nRF24L01_Breakout

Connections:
+3.3V: C21.1, C28.1, U14.2 (VCC); also elsewhere on the board
/MCU/A6: U14.3 (CE); also elsewhere on the board
/MCU/CLK: U14.5 (SCK); also elsewhere on the board
/MCU/MISO: U14.7 (MISO); also elsewhere on the board
/MCU/MOSI: U14.6 (MOSI); also elsewhere on the board
/MCU/PC3-A3: U14.4 (~CSN); also elsewhere on the board
GND: C21.2, C28.2, U14.1 (GND); also elsewhere on the board

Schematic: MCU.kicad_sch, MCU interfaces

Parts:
C22, C29: 100nF; C_0603_1608Metric
JP1, JP2, JP3, JP9, JP10, JP11, JP12, JP13, JP14, JP15, JP16, JP17, JP18, JP19, JP20, JP21, JP22, JP23, JP24, JP25, JP26, JP27, JP28: Jumper_2_Open; PinHeader_1x02_P1.27mm_Vertical
R108, R109: 4.7k; R_0603_1608Metric
T20, T21, T22, T23, T24, T25, T26, T27: TP; TestPoint_Pad_D1.0mm
U15: ATMEGA-328P; TQFP-32_7x7mm_P0.8mm

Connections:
+5V: C22.2, C29.2, R108.1, R109.1, U15.4 (VCC), U15.6 (VCC), U15.18 (AVCC); also elsewhere on the board
/Anemometer/SCL: JP19.2 (B), R109.2, T20.1; also elsewhere on the board
/Anemometer/SDA: JP18.2 (B), R108.2, T21.1; also elsewhere on the board
/Crystal/XTAl_1: U15.7 (XTAL1/PB6); also elsewhere on the board
/Crystal/XTAl_2: U15.8 (XTAL2/PB7); also elsewhere on the board
/DTR: JP20.2 (B); also elsewhere on the board
/GNSS_RX: JP27.2 (B); also elsewhere on the board
/GNSS_TX: JP26.2 (B); also elsewhere on the board
/MCU/A6: JP1.2 (B); also elsewhere on the board
/MCU/A7: JP3.2 (B); also elsewhere on the board
/MCU/CLK: JP13.2 (B), T24.1; also elsewhere on the board
/MCU/MISO: JP12.2 (B), T23.1; also elsewhere on the board
/MCU/MOSI: JP11.2 (B), T22.1; also elsewhere on the board
/MCU/PB0: JP2.2 (B), T25.1; also elsewhere on the board
/MCU/PB1-D9~: JP9.2 (B), T26.1; also elsewhere on the board
/MCU/PB2-D10~: JP10.2 (B), T27.1; also elsewhere on the board
/MCU/PC0-A0: JP14.2 (B); also elsewhere on the board
/MCU/PC1-A1: JP15.2 (B); also elsewhere on the board
/MCU/PC2-A2: JP16.2 (B); also elsewhere on the board
/MCU/PC3-A3: JP17.2 (B); also elsewhere on the board
/MCU/PD3-D3-(INT1)~: JP24.2 (B); also elsewhere on the board
/MCU/PD4-D4: JP25.2 (B); also elsewhere on the board
/MCU/PD5-D5~: JP28.2 (B); also elsewhere on the board
/MCU/RX: JP22.2 (B); also elsewhere on the board
/MCU/TX: JP21.2 (B); also elsewhere on the board
/WIND_INTERRUPT: JP23.2 (B); also elsewhere on the board
GND: C22.1, C29.1, U15.3 (GND), U15.5 (GND), U15.21 (GND); also elsewhere on the board
unnamed: JP1.1 (A), U15.19 (ADC6)
unnamed: JP2.1 (A), U15.12 (PB0)
unnamed: JP3.1 (A), U15.22 (ADC7)
unnamed: JP9.1 (A), U15.13 (PB1)
unnamed: JP10.1 (A), U15.14 (PB2)
unnamed: JP11.1 (A), U15.15 (PB3)
unnamed: JP12.1 (A), U15.16 (PB4)
unnamed: JP13.1 (A), U15.17 (PB5)
unnamed: JP14.1 (A), U15.23 (PC0)
unnamed: JP15.1 (A), U15.24 (PC1)
unnamed: JP16.1 (A), U15.25 (PC2)
unnamed: JP17.1 (A), U15.26 (PC3)
unnamed: JP18.1 (A), U15.27 (PC4)
unnamed: JP19.1 (A), U15.28 (PC5)
unnamed: JP20.1 (A), U15.29 (~RESET/PC6)
unnamed: JP21.1 (A), U15.30 (PD0)
unnamed: JP22.1 (A), U15.31 (PD1)
unnamed: JP23.1 (A), U15.32 (PD2)
unnamed: JP24.1 (A), U15.1 (PD3)
unnamed: JP25.1 (A), U15.2 (PD4)
unnamed: JP26.1 (A), U15.11 (PD7)
unnamed: JP27.1 (A), U15.10 (PD6)
unnamed: JP28.1 (A), U15.9 (PD5)

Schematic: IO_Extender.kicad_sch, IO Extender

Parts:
C11: 100nF; C_0603_1608Metric
D21: LED; LED_0603_1608Metric
R1: 330; R_0603_1608Metric
R110: 10k; R_0603_1608Metric
R111: 10k; R_0603_1608Metric; not fitted
T46: TP; TestPoint_Pad_D1.0mm
U17: PCA9536D; SOIC-8_3.9x4.9mm_P1.27mm
U28: ADS1115IDGS; TSSOP-10_3x3mm_P0.5mm

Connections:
+5V: C11.2, U17.8 (VDD); also elsewhere on the board
/Anemometer/SCL: U17.6 (SCL), U28.9 (SDA); also elsewhere on the board
/Anemometer/SDA: U17.7 (SDA), U28.10 (SCL); also elsewhere on the board
/CLK_POT_NUM/~CS_SD: U17.5 (IO3); also elsewhere on the board
/GNSS_ENABLED: U17.3 (IO2); also elsewhere on the board
/IO_Extender/+5V_Security: R111.1, U28.8 (VDD)
/IO_Extender/AIN1: U28.5 (AIN1)
/IO_Extender/AIN2: U28.6 (AIN2)
/IO_Extender/AIN3: U28.7 (AIN3)
/SIMULATE_WIND/~CS_NUM_POT: U17.2 (IO1); also elsewhere on the board
/Vcurrent: U28.4 (AIN0); also elsewhere on the board
GND: C11.1, R1.2, R110.2, U17.4 (VSS), U28.3 (GND); also elsewhere on the board
unnamed: D21.2 (A), U17.1 (IO0)
unnamed: D21.1 (K), R1.1
unnamed: R110.1, R111.2, U28.1 (ADDR)
unnamed: T46.1, U28.2 (ALERT/RDY)

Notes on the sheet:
SELF_TEST

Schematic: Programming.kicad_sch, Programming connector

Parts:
C23, C24, C41: 100nF; C_0603_1608Metric
D25: LED_USB; LED_0603_1608Metric
D26: TX_LED; LED_0603_1608Metric
D27: RX_LED; LED_0603_1608Metric
J3: USB_C_Receptacle_USB2.0_16P; USB_C_Receptacle_GCT_USB4085
R19, R54, R55: 270; R_0603_1608Metric
R67, R68: 0; R_0603_1608Metric
T14, T15, T16, T17, T18: TP; TestPoint_Pad_D1.0mm
U19: FT231XS; SSOP-20_3.9x8.7mm_P0.635mm
U20: USBLC6-2P6; SOT-666

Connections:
+5V: C23.1, C24.1, J3.A4 (VBUS), J3.A9 (VBUS), J3.B4 (VBUS), J3.B9 (VBUS), U19.14 (~RESET), U19.15 (VCC), U20.5 (VBUS); also elsewhere on the board
/DTR: C41.2; also elsewhere on the board
/MCU/RX: U19.4 (RXD); also elsewhere on the board
/MCU/TX: U19.20 (TXD); also elsewhere on the board
/Programming/+3.3V: D25.2 (A), U19.3 (VCCIO), U19.13 (3V3OUT)
GND: C23.2, C24.2, J3.A1 (GND), J3.A12 (GND), J3.B1 (GND), J3.B12 (GND), J3.S1 (SHIELD), R19.2, R54.2, R55.2, U19.6 (GND), U19.9 (~CTS), U19.16 (GND), U20.2 (GND); also elsewhere on the board
unnamed: D25.1 (K), R19.1
unnamed: D26.2 (A), U19.10 (CBUS2)
unnamed: D26.1 (K), R54.1
unnamed: D27.2 (A), U19.17 (CBUS1)
unnamed: D27.1 (K), R55.1
unnamed: J3.A6 (D+), J3.B6 (D+), R68.1
unnamed: J3.A7 (D-), J3.B7 (D-), R67.1
unnamed: R67.2, U20.4 (I/O2)
unnamed: R68.2, U20.6 (I/O1)
unnamed: T17.1, U19.18 (CBUS0)
unnamed: U19.12 (USBDM), U20.3 (I/O2)
unnamed: U19.11 (USBDP), U20.1 (I/O1)
unnamed: T15.1, U19.8 (~DCD)
unnamed: T14.1, U19.7 (~DSR)
unnamed: C41.1, U19.1 (~DTR)
unnamed: T16.1, U19.5 (~RI)
unnamed: T18.1, U19.2 (~RTS)

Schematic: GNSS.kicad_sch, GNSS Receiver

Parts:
AE1: Internal_antenna; MountingHole_2.2mm_M2_DIN965_Pad
C7, C36: 100nF; C_0603_1608Metric
C9, C10, C34: 120pF; C_0603_1608Metric
C25, C26: 330pF; C_0603_1608Metric
C35: 1nF; C_0603_1608Metric
D2: POS_ENABLE; LED_0603_1608Metric
D24: GNSS_USB; LED_0603_1608Metric
D28: LED_EXT_ANTENNA; LED_0603_1608Metric
D34: GNSS_BATT; LED_0603_1608Metric
D36: 1N4148; D_SOD-323
J5: USB_C_Receptacle_USB2.0_16P; USB_C_Receptacle_GCT_USB4085
J10: 132415; SMA_Molex_73251-1153_EdgeMount_Horizontal
L6: 56nH; L_0603_1608Metric
L9: 39nH; L_0603_1608Metric
Q1: SI2302; SOT-23
Q10: CJ3401; SOT-23
Q11: 2N7002; SOT-23
R11, R12, R15, R69, R70, R71, R72, R94, R106, R107: 0; R_0603_1608Metric
R13, R14, R58: 1k; R_0603_1608Metric
R16, R73, R74, R95: 330; R_0603_1608Metric
R17: R_680K_SMD_0603; R_0603_1608Metric
R56: 100k; R_0603_1608Metric
R57: 10k; R_0603_1608Metric
R92: R_100K_SMD_0603; R_0603_1608Metric
R93: R_1K_SMD_0603; R_0603_1608Metric
T1, T4, T5, T7, T8, T33, T34, T38, T40, T52: TP; TestPoint_Pad_D1.0mm
U3: NEO-M8M; ublox_NEO
U21: AS193-73LF; SOT-23-6
U26: USBLC6-2P6; SOT-666
U27: LP2985-3.3; SOT-23-5

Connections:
+3.3V_GNSS: C7.2, D28.2 (A), Q10.2 (S), R58.1, R93.2, U3.8 (~RESET); also elsewhere on the board
+VCap_GNSS: U3.22 (V_BCKP); also elsewhere on the board
/GNSS/D+: U3.6 (USB_DP), U26.3 (I/O2)
/GNSS/D-: U3.5 (USB_DM), U26.1 (I/O1)
/GNSS/VBus: J5.A4 (VBUS), J5.A9 (VBUS), J5.B4 (VBUS), J5.B9 (VBUS), R71.1, U26.5 (VBUS)
/GNSS/VCC_RF: L9.2, R17.2, U3.9 (VCC_RF)
/GNSS/VCC_USB: C36.1, D36.2 (A), R72.2, U3.7 (VDD_USB), U27.5 (VOUT)
/GNSS/~ANTENNA_DETECT: C26.1, L6.1, Q1.1 (G), R17.1, R57.2, T52.1, U21.6 (V1)
/GNSS_ENABLED: R107.2; also elsewhere on the board
/GNSS_RX: R12.1; also elsewhere on the board
/GNSS_TX: R11.1; also elsewhere on the board
GND_GNSS: C7.1, C25.1, C26.2, C35.2, C36.2, D2.1 (K), D24.1 (K), D34.1 (K), J5.A1 (GND), J5.A12 (GND), J5.B1 (GND), J5.B12 (GND), J5.S1 (SHIELD), J10.2 (Ext), Q1.3 (D), Q11.2 (S), R14.1, R57.1, R92.1, U3.10 (GND), U3.12 (GND), U3.13 (GND), U3.24 (GND), U21.2 (GND), U26.2 (GND), U27.2 (GND); also elsewhere on the board
unnamed: AE1.1 (A), C10.2
unnamed: C25.2, L6.2, R56.2
unnamed: D2.2 (A), R16.1
unnamed: D24.2 (A), R73.1
unnamed: D28.1 (K), R74.2
unnamed: D34.2 (A), R95.1
unnamed: D36.1 (K), Q11.1 (G), R92.2, R107.1
unnamed: J5.A6 (D+), J5.B6 (D+), R69.1
unnamed: J5.A7 (D-), J5.B7 (D-), R70.1
unnamed: C34.2, J10.1 (In), L9.1, R56.1
unnamed: Q1.2 (S), R58.2, R106.2, T1.1, U21.4 (V2)
unnamed: Q10.3 (D), R94.2, T40.1, U3.23 (VCC)
unnamed: Q10.1 (G), Q11.3 (D), R93.1
unnamed: R12.2, R13.1
unnamed: R15.1, R16.2
unnamed: R69.2, U26.4 (I/O2)
unnamed: R70.2, U26.6 (I/O1)
unnamed: R72.1, R73.2
unnamed: R94.1, R95.2
unnamed: R74.1, R106.1
unnamed: T38.1, U3.2 (D_SEL)
unnamed: T8.1, U3.4 (EXTINT)
unnamed: C9.2, U3.11 (RF_IN)
unnamed: R13.2, R14.2, T4.1, U3.21 (RXD/SPI_MOSI)
unnamed: T34.1, U3.19 (SCL/SPI_CLK)
unnamed: T33.1, U3.18 (SDA/~SPI_CS)
unnamed: R15.2, U3.3 (TIMEPULSE)
unnamed: R11.2, T5.1, U3.20 (TXD/SPI_MISO)
unnamed: T7.1, U3.1 (~SAFEBOOT)
unnamed: C9.1, U21.5 (J1)
unnamed: C10.1, U21.1 (J2)
unnamed: C34.1, U21.3 (J3)
unnamed: C35.1, U27.4 (BP)
unnamed: R71.2, U27.1 (VIN), U27.3 (ON/~OFF)

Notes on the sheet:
V_{RX}=5*${a52a78e2-18e3-4ec6-8d46-591b24bd5bd1:VALUE}/(${a52a78e2-18e3-4ec6-8d46-591b24bd5bd1:VALUE}+${f5d83104-4b79-4b80-ade9-bfd7c6659042:VALUE})
EXT_ANTENNA

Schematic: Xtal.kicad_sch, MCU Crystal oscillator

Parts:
C5, C6: 22pF; C_0603_1608Metric
Y1: 16MHz; Crystal_SMD_HC49-SD

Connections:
/Crystal/XTAl_1: C5.2, Y1.2; also elsewhere on the board
/Crystal/XTAl_2: C6.2, Y1.1; also elsewhere on the board
GND: C5.1, C6.1; also elsewhere on the board

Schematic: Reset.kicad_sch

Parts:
J11: KF128-2.54_2P; TerminalBlock_Phoenix_MPT-0,5-2-2.54_1x02_P2.54mm_Horizontal
R46: 10k; R_0603_1608Metric
SW4: PB_SMD_12V_50MA_6MM_6MM; SW_Push_1P1T_NO_CK_KSC7xxJ

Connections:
+5V: R46.1; also elsewhere on the board
/DTR: J11.2, R46.2, SW4.2 (B); also elsewhere on the board
GND: J11.1, SW4.1 (A); also elsewhere on the board

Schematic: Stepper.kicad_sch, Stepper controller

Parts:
C30: 100nF; C_0603_1608Metric
C31, C32: XX; C_0603_1608Metric
D22, D35: 1N4148; D_SOD-323
IC1: L6208; ST_PowerSSO-36_SlugDown_ThermalVias
J16: Stepper; PhoenixContact_MSTBA_2,5_4-G-5,08_1x04_P5.08mm_Horizontal
J22: KF128-2.54_2P; TerminalBlock_Phoenix_MPT-0,5-2-2.54_1x02_P2.54mm_Horizontal
J26: +24V; PhoenixContact_MSTBA_2,5_2-G-5,08_1x02_P5.08mm_Horizontal
J31: Motor_Control_Pull_Up; TerminalBlock_Phoenix_MPT-0,5-3-2.54_1x03_P2.54mm_Horizontal
J32: KF128-2.54_3P; TerminalBlock_Phoenix_MPT-0,5-3-2.54_1x03_P2.54mm_Horizontal
R64, R97, R99, R101: 10k; R_0603_1608Metric
R65, R66: XX; R_0603_1608Metric
R79, R80: 0.33; R_Axial_DIN0414_L11.9mm_D4.5mm_P15.24mm_Horizontal
R84, R85, R86, R87, R88, R89: 220; R_0603_1608Metric
R98, R100: 10k; R_0603_1608Metric; not fitted
R103: 0; R_0603_1608Metric
RV2: Vref_B; Potentiometer_Bourns_3314S_Horizontal
RV3: Vref_A; Potentiometer_Bourns_3314S_Horizontal
T3, T28, T29, T30, T31, T32, T42: TP; TestPoint_Pad_D1.0mm
U23, U24, U25: PC817XI; SOP-4_4.4x2.6mm_P1.27mm

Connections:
+5V: J31.1, J31.2, J31.3, R84.2, R85.2, R86.2, R87.1, R88.1, R89.1, R97.1, R99.1, R103.2, RV2.3, RV3.3; also elsewhere on the board
+24V: D35.2 (A), IC1.17 (VS_B), IC1.20 (VS_A), J26.2; also elsewhere on the board
/MCU/A7: J22.2, R64.2; also elsewhere on the board
/MCU/PB0: U24.2; also elsewhere on the board
/MCU/PB1-D9~: U25.2; also elsewhere on the board
/MCU/PB2-D10~: U23.2; also elsewhere on the board
/Stepper/CONTROL: IC1.13 (CONTROL), R97.2, R98.1, T42.1
/Stepper/HALF/FULL: IC1.12 (HALF/FULL), R99.2, R100.1, T3.1
/Stepper/RC_1: C31.1, IC1.4 (RCA), R65.2, T28.1
/Stepper/RC_2: C32.1, IC1.9 (RCB), R66.2, T29.1
/Stepper/SENSE_A: IC1.3 (SENSE_A), R80.1
/Stepper/SENSE_B: IC1.10 (SENSE_B), R79.1
/Stepper/STEP_CW: IC1.2 (CW/CWW), J32.1, R88.2, T31.1, U24.4
/Stepper/STEP_ENABLE: IC1.14 (EN), J32.2, R87.2, T32.1, U25.4
/Stepper/STEP_PULSE: IC1.1 (CLOCK), J32.3, R89.2, T30.1, U23.4
/Stepper/Vref_A: IC1.24 (VREF_A), RV3.2
/Stepper/Vref_B: IC1.11 (VREF_B), RV2.2
GND: C31.2, C32.2, IC1.6, IC1.7, IC1.18, IC1.19, IC1.23 (RESET), J22.1, J26.1, R65.1, R66.1, R79.2, R80.2, R98.2, R100.2, RV2.1, RV3.1, U23.3, U24.3, U25.3; also elsewhere on the board
unnamed: C30.2, R101.2
unnamed: C30.1, D22.2 (A), D35.1 (K)
unnamed: D22.1 (K), IC1.15 (VBOOT)
unnamed: IC1.5 (OUT1A), J16.1
unnamed: IC1.8 (OUT1B), J16.3
unnamed: IC1.21 (OUT2A), J16.2
unnamed: IC1.16 (OUT2B), J16.4
unnamed: IC1.22 (VCP), R101.1
unnamed: R84.1, U23.1
unnamed: R85.1, U24.1
unnamed: R86.1, U25.1
unnamed: R64.1, R103.1

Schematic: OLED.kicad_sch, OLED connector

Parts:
J8: I2C_Selector; PinHeader_2x03_P2.54mm_Vertical
J9: OLED_SOCKET; PinSocket_1x04_P2.54mm_Vertical

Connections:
+5V: J9.3; also elsewhere on the board
/Anemometer/SCL: J8.5, J8.6; also elsewhere on the board
/Anemometer/SDA: J8.1, J8.2; also elsewhere on the board
/OLED/A: J8.4, J9.1
/OLED/B: J8.3, J9.2
GND: J9.4; also elsewhere on the board

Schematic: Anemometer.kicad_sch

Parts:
J18: KF128-2.54_4P; TerminalBlock_Phoenix_MPT-0,5-4-2.54_1x04_P2.54mm_Horizontal
T43, T45: TP; TestPoint_Pad_D1.0mm

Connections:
+5V: J18.1; also elsewhere on the board
/Anemometer/SCL: J18.3, T45.1; also elsewhere on the board
/Anemometer/SDA: J18.2, T43.1; also elsewhere on the board
GND: J18.4; also elsewhere on the board

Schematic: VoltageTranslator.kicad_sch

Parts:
C39: 100nF; C_0603_1608Metric
U18: LVC125A; SSOP-14_5.3x6.2mm_P0.65mm

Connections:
+3.3V: C39.1, U18.14 (VCC); also elsewhere on the board
/CLK_POT_NUM/~CS_SD: U18.2; also elsewhere on the board
/MCU/CLK: U18.9; also elsewhere on the board
/MCU/MISO: U18.11; also elsewhere on the board
/MCU/MOSI: U18.5; also elsewhere on the board
/SD_Reader/VoltageTranslator/1Y: U18.3; also elsewhere on the board
/SD_Reader/VoltageTranslator/2Y: U18.6; also elsewhere on the board
/SD_Reader/VoltageTranslator/3Y: U18.8; also elsewhere on the board
/SD_Reader/VoltageTranslator/4A: U18.12; also elsewhere on the board
GND: C39.2, U18.1, U18.4, U18.7 (GND), U18.10, U18.13; also elsewhere on the board

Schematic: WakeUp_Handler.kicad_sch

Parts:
D30, D32: 1N4148; D_SOD-323
J35, J36: KF128-2.54_2P; TerminalBlock_Phoenix_MPT-0,5-2-2.54_1x02_P2.54mm_Horizontal
Q9: 2N7002; SOT-23
R75, R76, R81, R82, R83: 10k; R_0603_1608Metric
RV1: Light_Reference; Potentiometer_Bourns_3314S_Horizontal
SW7: PB_SMD_12V_50MA_6MM_6MM; SW_Push_1P1T_NO_CK_KSC7xxJ
T35, T36, T44, T50, T51: TP; TestPoint_Pad_D1.0mm
U29: LM358DR; TSSOP-8_4.4x3mm_P0.65mm

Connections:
+5V_Security: J35.2, J36.1, R76.2, RV1.3, SW7.2 (B), U29.8 (V+); also elsewhere on the board
/Power_Supply/WakeUp_Handler/PS_CTRL: Q9.3 (D), R76.1, T36.1; also elsewhere on the board
/Power_Supply/WakeUp_Handler/WIND_INTERRUPT: D30.2 (A); also elsewhere on the board
GND_Security: Q9.2 (S), R75.1, R83.1, RV1.1, U29.4 (V-); also elsewhere on the board
unnamed: D30.1 (K), D32.1 (K), Q9.1 (G), R82.2, R83.2, T50.1, U29.1
unnamed: D32.2 (A), J36.2, SW7.1 (A), T51.1
unnamed: J35.1, R75.2, R81.1, T35.1
unnamed: R81.2, R82.1, U29.3 (+)
unnamed: RV1.2, T44.1, U29.2 (-)

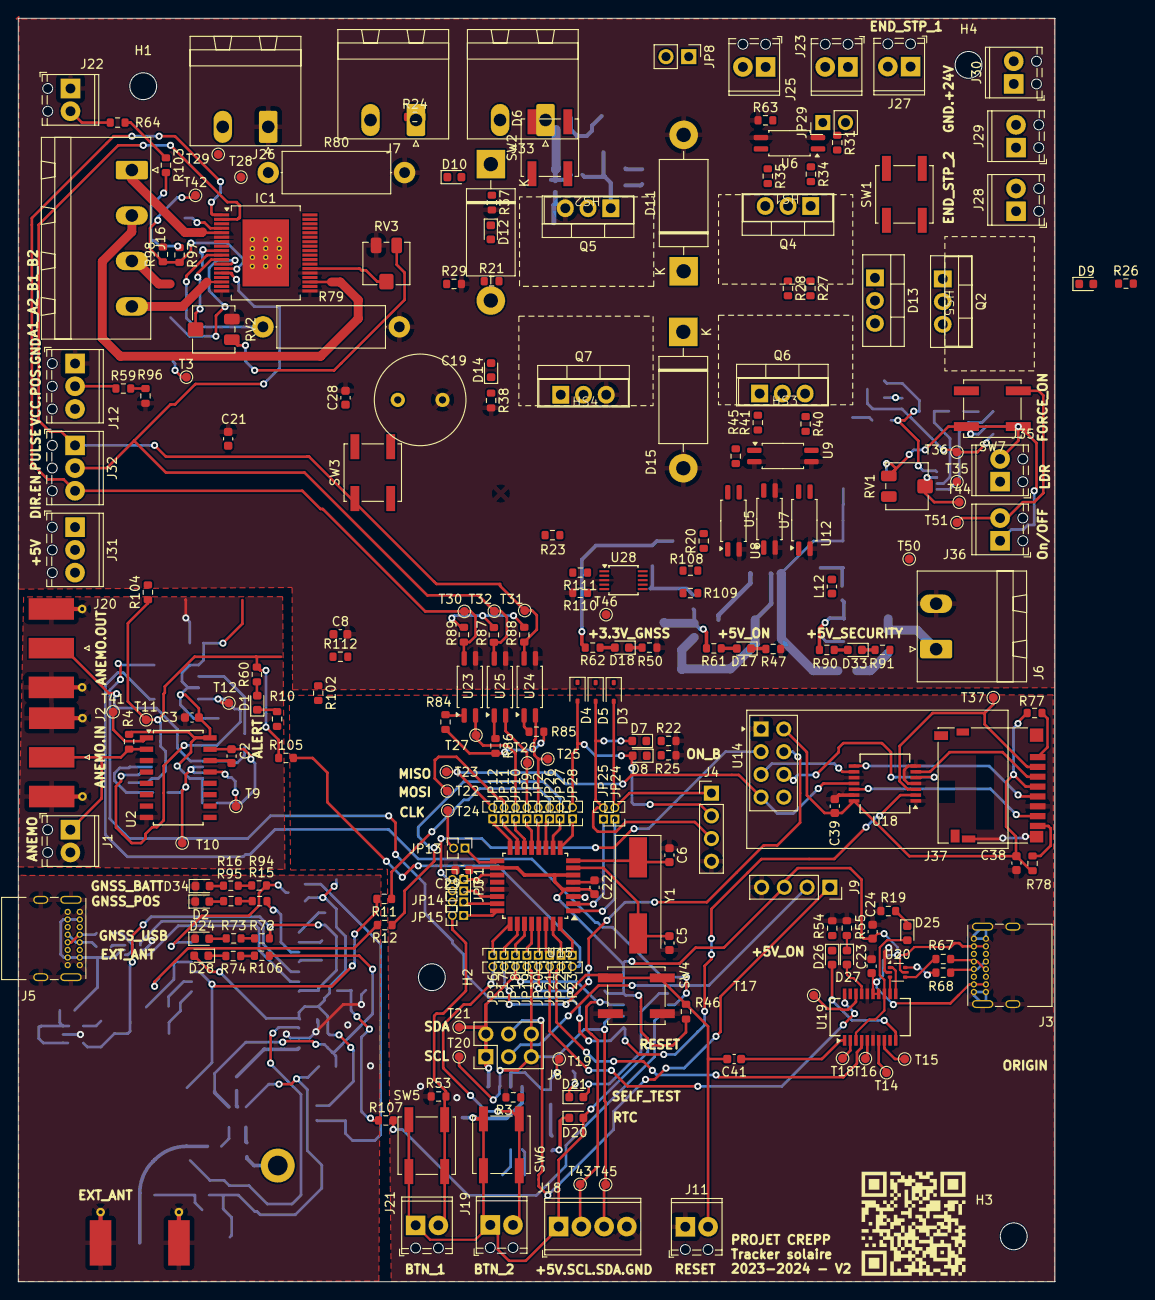
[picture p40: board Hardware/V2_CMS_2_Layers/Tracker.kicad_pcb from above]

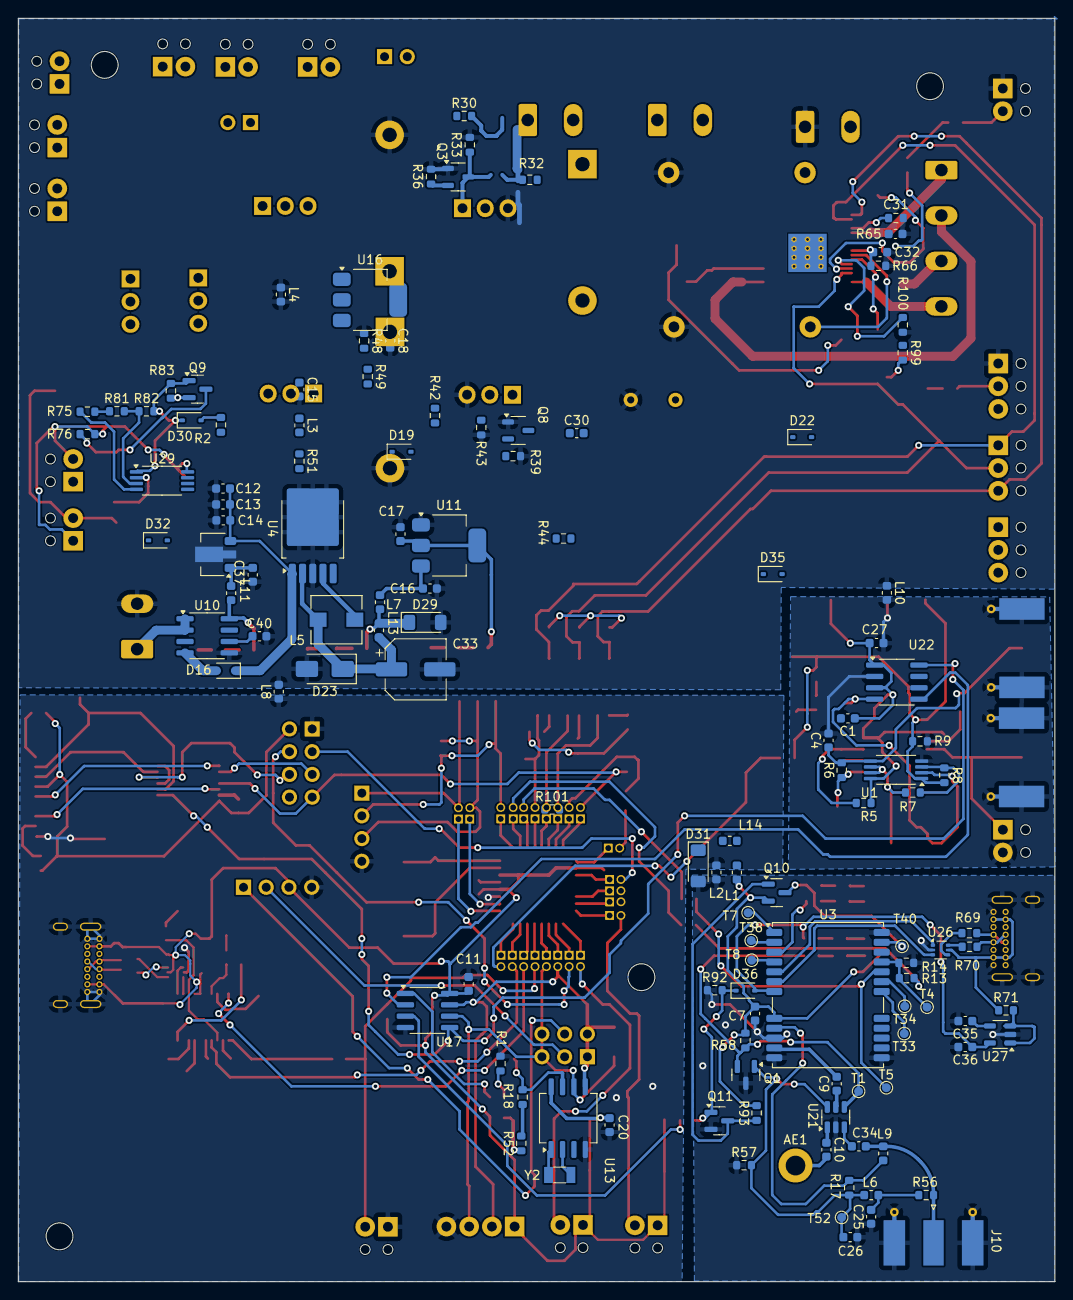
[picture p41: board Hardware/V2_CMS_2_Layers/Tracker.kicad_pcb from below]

Board: 2 copper layers, 115.8 x 141.2 mm, 367 parts (123 on the bottom side), 235 nets.

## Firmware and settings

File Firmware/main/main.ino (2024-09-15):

//#include <SoftwareSerial.h>
//#include <SoftwareSerial.h>
//#include "ConnectionPins.h"
//#include "commonTypes.h"
//#include "SunPos.h"

#include "AzimutMotor.h"


#include "Settings.h"

#include "Display.h"
#include "ADC_Tools.h"
#include "ConnectionPins.h"

#include "SunTracker.h"
#include "GNSS_Coordinates.h"
#include "GNSS_Time.h"
#include "GNSS.h"                                                    
#include <TinyGPSPlus.h>

#include "PCA9536.h"

#define BLINK_EN_A digitalWrite(4,1);delay(100);digitalWrite(4,0);delay(100);
#define BLINK_EN_B digitalWrite(5,1);delay(100);digitalWrite(5,0);delay(100);


#include <Wire.h>

#include <Wire.h>
#include <RTClib.h>
// Création d'une instance TinyGPS++
TinyGPSPlus gps;
PCA9536 io_Extender;

// Création d'une instance SoftwareSerial pour communiquer avec le module GPS
SoftwareSerial ss(7,6); // RX, TX


#define PCA9536_ADDRESS 0x41 // Adresse I2C du PCA9536D



//#include "ElevationMotor.h"



#define CHANNEL_POT 1


//ElevationMotor ElevMotor(elevEnable, elevIN_A, elevIN_B, elevPotar );
AzimutMotor AzimMotor(tb66EnaPin,tb66PulsePin,tb66DirPin,tb66ButeePin);

Display terminal(128,32, 0x3C);
ADC_Tools adc;

CityLocalisation city = {0,0, 0, 0};
SunTracker sunTracker(city);

//GNSS gnss(7, 6, 9600);

RTC_DS1307 rtc;


/*!
*/
GNSS_Date gnss_date;
GNSS_Time gnss_time;
GNSS_Coordinates gnss_coordinates;



 void setup()
 {

    Serial.begin(9600);
    io_Extender.begin();
    //


    Serial.println("INIT : OK");
    ss.begin(9600);
    terminal.init();
    Wire.begin();  // Initialisation du bus I2C

    pinMode(4,OUTPUT);
    pinMode(5,OUTPUT);


    BLINK_EN_A;
    BLINK_EN_B;

    
   
    //gnss.init();
    // gnss.startGNSS();
    //gnss.setDebugChannel(&Serial, 9600);

    //configurePCA9536(0x00);

    //rtc.writeSqwPinMode(DS1307_SquareWave1HZ);
    io_Extender.pinMode(PCA9536_PIN_0,PCA9536_OUTPUT);

    io_Extender.digitalWrite(PCA9536_PIN_0,PC9536_HIGH);

    terminal.println("SELF-TEST : OK");
    Serial.println("SELF-TEST : OK");
    //writePCA9536(0x0F); // Met toutes les broches en état haut (HIGH)
    delay(500);
    io_Extender.digitalWrite(PCA9536_PIN_0,PC9536_LOW);
    //writePCA9536(0x00); // Met toutes les broches en état bas (LOW)

    delay(100);

    Serial.println("RTC : OK");
    rtc.begin();
    delay(100);
    rtc.writeSqwPinMode(DS1307_SquareWave1HZ); // Configurer pour une onde carrée de 1 Hz


    terminal.println("WAITING GNSS..");

    while (ss.available() > 0) {
    gps.encode(ss.read()); // Transfert des données au parser TinyGPS++

    // Si une nouvelle localisation est disponible
    if (gps.location.isUpdated()) {
      Serial.print("Latitude  : ");
      Serial.println(gps.location.lat(), 6);
      Serial.print("Longitude : ");
      Serial.println(gps.location.lng(), 6);
    }

    // Si une nouvelle information temporelle est disponible
    if (gps.time.isUpdated()) {
      Serial.print("Heure     : ");
      Serial.print(gps.time.hour());
      Serial.print(":");
      Serial.print(gps.time.minute());
      Serial.print(":");
      Serial.println(gps.time.second());
    }

    // Si une nouvelle altitude est disponible
    if (gps.altitude.isUpdated()) {
      Serial.print("Altitude  : ");
      Serial.print(gps.altitude.meters());
      Serial.println(" m");
    }

    // Si une nouvelle vitesse est disponible
    if (gps.speed.isUpdated()) {
      Serial.print("Vitesse   : ");
      Serial.print(gps.speed.kmph());
      Serial.println(" km/h");
    }

    Serial.println();
  }

  
    // while( (gnss_time.hour == 0) || (gnss_time.minute == 0))
    // {
      
    //   //gnss_time = gnss.getTime();
    // }
   //gnss.readData();
    Serial.println("END");
    //terminal.println("TIME");
    //terminal.println(String(gnss_date.day)+"/"+String(gnss_date.month)+"/"+String(gnss_date.year)+" - "+ String(gnss_time.hour)+":"+String(gnss_time.minute));




    //Position OK

    
    // bool isReady = false;


    // while( isReady == false)
    // {
    //   gnss.readData();
    //   isReady = gnss.isReady();
    //   BLINK_EN_A;
    //   delay(1000);
    //   BLINK_EN_A;
    //   delay(1000);
    //   BLINK_EN_A;
    //   delay(1000);
    //   BLINK_EN_B;
    //   delay(200);
    //   BLINK_EN_A;
    //   delay(500);
    // }   
    // gnss_coordinates = gnss.getCoordinates();

    // terminal.println(String(gnss_coordinates.latitude,5)+String(gnss_coordinates.latitudeDirection));
    // terminal.println(String(gnss_coordinates.longitude,5)+String(gnss_coordinates.longitudeDirection));
  

 }

 void loop()
 {

  static bool isRunning = false;

    if(analogRead(A1)>800)
    {
      AzimMotor.enableDevice();
      AzimMotor.makeSteps(400, DIRECTION_EST) ;
      //terminal.println("Est");
    }
    else if(analogRead(A1)<200)
    {
      AzimMotor.enableDevice();
       AzimMotor.makeSteps(400, DIRECTION_WEST) ;
       //terminal.println("West");
    }
    else
    {
      AzimMotor.disableDevice();
    }
    //delay(500);

    //BLINK_EN_A;
 }


// void configurePCA9536(uint8_t config) {
//   Wire.beginTransmission(PCA9536_ADDRESS);
//   Wire.write(PCA9536_CONFIG);  // Sélection du registre de configuration
//   Wire.write(config);          // Écrire la configuration (0x00 : toutes les broches en sortie)
//   Wire.endTransmission();
// }

// // Fonction pour écrire des données sur le port de sortie du PCA9536
// void writePCA9536(uint8_t value) {
//   Wire.beginTransmission(PCA9536_ADDRESS);
//   Wire.write(PCA9536_OUTPUT_PORT);  // Sélection du registre de sortie
//   Wire.write(value);                // Écrire la valeur (0x0F pour activer toutes les broches)
//   Wire.endTransmission();
// }

// Fonction pour lire l'état des broches d'entrée du PCA9536
// uint8_t readPCA9536() {
//   Wire.beginTransmission(PCA9536_ADDRESS);
//   Wire.write(PCA9536_INPUT_PORT);  // Sélection du registre d'entrée
//   Wire.endTransmission();

//   Wire.requestFrom(PCA9536_ADDRESS, 1);
//   return Wire.read();  // Lire l'état des broches
// }


/*
#define SCREEN_WIDTH 128 // OLED display width, in pixels
#define SCREEN_HEIGHT 64 // OLED display height, in pixels

// Declaration for an SSD1306 display connected to I2C (SDA, SCL pins)
// The pins for I2C are defined by the Wire-library. 
// On an arduino UNO:       A4(SDA), A5(SCL)
// On an arduino MEGA 2560: 20(SDA), 21(SCL)
// On an arduino LEONARDO:   2(SDA),  3(SCL), ...
#define OLED_RESET     -1 // Reset pin # (or -1 if sharing Arduino reset pin)
#define SCREEN_ADDRESS 0x3C ///< See datasheet for Address; 0x3D for 128x64, 0x3C for 128x32
Adafruit_SSD1306 display(SCREEN_WIDTH, SCREEN_HEIGHT, &Wire, OLED_RESET);
*/

/*
long GPS_Speed=9600;
uint8_t myGPS_RX=2;  // broche RX pour l'arduino
uint8_t myGPS_TX=3;  // broche TX pour l'arduino

// pour le vérin d'élévation pint en H
uint8_t elevEnable=5;   // broche Enable - output Active High
uint8_t elevIN_A=6;     // broche IN_A - output Active High
uint8_t elevIN_B=7;     // broche IN_B - output Active High

uint8_t  elevPotar=A0;  // mesure du potentiomètre Input Analog 

*/
/*




ElevationMotor ElevMotor(elevEnable, elevIN_A, elevIN_B, elevPotar );
*/
/* AzimutMotor::AzimutMotor(uint8_t enaPin, uint8_t pulsePin, uint8_t dirPin, uint8_t buteePin)
uint8_t tb66DirPin = 8;  // Broche Dir   - output Active High
uint8_t tb66PulsePin = 9; // Broche Pulse  - output Active High
uint8_t tb66EnaPin = 10; // broche Enable -  - output Active High

uint8_t tb66ButeePin=11;  // Broche Capteur fin de course Retour - Active Low

AzimutMotor AzimMotor(tb66EnaPin,tb66PulsePin,tb66DirPin,tb66ButeePin);

SunPos mySunPos;

date_t dateret;
time_t timeret;
location_t locret;
orientation_t orientationret;
float daynum;
char affString[80];

int myTimezone=0;

int prochaine_minute=0;
int interval=10;
bool premier_lancement=true;

float elevationCalcul = 30.0;
float azimutCalcul=0.0;

int localpas=0;

void prochain_trt(){
  prochaine_minute = (timeret.minute + interval) %60;
  sprintf(affString,"**************   prochain trt à %02d *******************",prochaine_minute);
  Serial.println(affString);
  Serial.flush();
}


void setup(){

  float aa=90.0;
 
  Serial.begin(115200);
  // oledinit();
  delay(200);

  //elevationCalcul = ElevMotor.setAngle(30.0);

  //localpas = AzimMotor.versOuest(200);
  //delay(2000);
  localpas = AzimMotor.retourEst();
  delay(2000);
  azimutCalcul = AzimMotor.getAngle();
  Serial.println(azimutCalcul,2);
  delay(2000);
/*
  tests
  for (int i=1;i<7;i++){
    aa=90.5 + i*30.0;
    Serial.println(aa,2);

    azimutCalcul = AzimMotor.setAngle(aa);

      delay(2000);
  }
*/
/*

};

void loop() {

  Serial.println(" - - - - - - - - \n");

 
  //oledaffClear();

timeret  = myNeo6m.getTime();
    //  oledaffHeure(timeret);
      sprintf(affString,"H: %02d:%02d:%02d  prochain à %02d",timeret.hour,timeret.minute,timeret.seconde,prochaine_minute);
      Serial.println(affString);



 dateret = myNeo6m.getDate();
      // oledaffDate(dateret);
      sprintf(affString,"D: %4d/%02d/%02d",dateret.year,dateret.month,dateret.day);
      Serial.println(affString);

  locret = myNeo6m.getLocation();
      // oledaffLocation(locret);
      Serial.print("Lat:");
      Serial.print(locret.lat,3);
      Serial.print("  Lng:");
      Serial.println(locret.lng,3);

  

  
  // daynum = mySunPos.calcDaynum(dateret, timeret);


  orientationret = mySunPos.calcOrientation(locret, dateret, timeret,myTimezone);
     // oledaffOrientation(orientationret);
       Serial.print("Azm:");
      Serial.print(orientationret.azimuth,2);
      Serial.print("  elv:");
      Serial.println(orientationret.elevation,2);

  if (premier_lancement) {
    prochain_trt();
     Serial.print("premiere Elevation : ");
    Serial.println(orientationret.elevation,2);
    // elevationCalcul = ElevMotor.setAngle(orientationret.elevation);
    azimutCalcul = AzimMotor.setAngle(orientationret.azimuth);
    premier_lancement = false;

  }

  if (timeret.minute == prochaine_minute) {
    // prochaine opération planfifiée
    prochain_trt();

    Serial.print("elevation.setAngle() ");
    Serial.println(orientationret.elevation,2);
    Serial.flush();
    // elevationCalcul = ElevMotor.setAngle(orientationret.elevation);

    azimutCalcul = AzimMotor.setAngle(orientationret.azimuth);
    

    Serial.print("azimuth.setAngle() ");
    Serial.println(orientationret.azimuth,2);
    Serial.flush();

    }
  

  Serial.print(" Angle :");
  Serial.println(AzimMotor.getAngle(),2);
  Serial.print(" Pas :");
  Serial.print(AzimMotor.getPas());
  Serial.print(" - micros ");
  Serial.println(micros());
  Serial.flush();

  //for(;;);

  delay(10000);

  };

  */

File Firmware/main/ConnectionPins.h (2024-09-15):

// cette librairie définit toutes les pins utilisées

#ifndef CONNECTION_PIN_h
#define CONNECTION_PIN_h

// pour le GPS
long GPS_Speed=9600;
uint8_t myGPS_RX=1;  // broche RX pour l'arduino
uint8_t myGPS_TX=0;  // broche TX pour l'arduino

//eventuellement pour avoir des traces dans le gps
//#define DEBUG_GP


// pour le vérin d'élévation pint en H
uint8_t elevEnable=5;   // broche Enable - output Active High
uint8_t elevIN_A=4;     // broche IN_A - output Active High
uint8_t elevIN_B=5;     // broche IN_B - output Active High

uint8_t  elevPotar=A0;  // mesure du potentiomètre Input Analog 
uint8_t userPot = A1;


//pour le TB6600 d'azimuth
//controle du tb6600
uint8_t tb66DirPin = 9;  // Broche Dir   - output Active High
uint8_t tb66PulsePin = 10; // Broche Pulse  - output Active High
uint8_t tb66EnaPin = 8; // broche Enable -  - output Active High

uint8_t tb66ButeePin=A2;  // Broche Capteur fin de course Retour - Active High

// oled - Par defaut c'est reconnu par la librairie Wire, donc on s'assure que les pattes ne sont pas utilisées

uint8_t oled_SCL=A5; 
uint8_t oled_SDA=A4; 






#endif

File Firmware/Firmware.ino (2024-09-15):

/*!
  Libraries 
*/
#include "Arduino.h"

//#include "DateTime.h"
#include "GNSS_Coordinates.h"
#include "GNSS_Time.h"

/**
 * @brief 
 * 
 */

typedef enum
{
  WinterHour = 1,
  SummerHour = 2
} SeasonHour;

typedef struct 
{
  int latitudeDeg;
  int latitudeMin;
  int longitudeDeg;
  int longitudeMin;

} CityLocalisation;


/*!

*/
class SunTracker
{
  public : 

    /**
     * @brief Construct a new Sun Tracker object
     * 
     * @param cityLocalisation 
     */
    SunTracker(CityLocalisation cityLocalisation);

    void setLocalisation(GNSS_Coordinates gnss_coordinates);

    /**
     * @brief Set the Debug object
     * 
     * @param debugState : debug state (True or False)
     */
    void setDebug(bool debugState);

    /**
     * @brief Update the azimuth and elevetion of sun for a given day 
     * 
     * @param indexOfDay 
     * @param datetime 
     */
    void update(uint16_t indexOfDay, GNSS_Time gnss_time);

    void debug(uint16_t rank);


    uint16_t convertDayInRank(GNSS_Date gnss_date) ;



    float getElevation(GNSS_Time gnss_time);
    float getAzimut(GNSS_Time gnss_time);
    


    float elevation = 0.0;
    float azimut = 0.0;
    
  private:

    CityLocalisation _cityLocalisation;

    bool _debugState = false;

    float _declination = 0.0;
    float _hourAngle = 0.0;
    uint16_t _indexOfDay = 0.0;

    SeasonHour _seasonHour = SeasonHour::WinterHour;
    

    float getDeclination();
    float getHourAngle(GNSS_Time gnss_time);
    float getRealTime(GNSS_Time gnss_time);
    float getEquationTime();

    
    
};



#include "Arduino.h"

#define RED 0
#define GREEN 1
#define BLUE 2
#define CYAN 3
#define ORANGE 4
#define WHITE 5
#define PURPLE 6
#define TURQUOISE 7
#define YELLOW 8
#define MAGENTA 9
#define ROSE 10

/**
 * @brief RGB class
 * 
 */
class RGB 			
{
public:

/**
 * @brief Construct a new RGB object
 * 
 * @param pin_red 
 * @param pin_green 
 * @param pin_blue 
 */
RGB(int pin_red, int pin_green, int pin_blue);	

/**
 * @brief Power on RGB LED with color
 * 
 * @param color 
 */
void on(int color);

/**
 * @brief Blink RGB LED
 * 
 * @param color 
 * @param delai_high 
 * @param delai_low 
 * @param nombre 
 */
void blink(int color, unsigned long delai_high, unsigned long delai_low,unsigned long nombre);

/**
 * @brief Power off RGB LED
 * 
 */
void off();

/**
 * @brief Function to display random colors
 * 
 * @param delai : delay in ms 
 * @param frequence : in Hz
 */
void randomRGB(unsigned long delai, int frequence);

private:

int pin_redIN;
int pin_greenIN;
int pin_blueIN;

}; 

#include "GNSS.h"

#include "Pinout.h"
#include "Settings.h"


CityLocalisation city = {0,0, 0, 0};

SunTracker sunTracker(city);


//RGB led(RGB_RED_PIN,RGB_GREEN_PIN,RGB_BLUE_PIN); 

GNSS gnss(GNSS_RX, GNSS_TX, 9600);

void setup() 
{

  //pinMode(13, OUTPUT);
  
  /*Serial.begin(9600);
  gnss.setDebugChannel(&Serial, 9600);
  gnss.setDebugState(true);*/

  gnss.init();

  gnss.startGNSS();

  //delay(1000);

  //gnss.stopGNSS();

  //gnss.startSelfTest();
  

  if(gnss.isReady())
  {
    Serial.println("<GNSS> OK");
  }
  else {
    Serial.println("<GNSS> FAIL");
  }


}

void loop() {
  
  

  //gnss.readData();


  //if(gnss.isValidPosition())
 // {
    
    //Serial.println("COORDINATES FOUND !");

    /*Serial.println(gnss.getCoordinates().latitude,5);
    Serial.println(gnss.getCoordinates().longitude,5);
    //Serial.println(gnss.getDate().day);
    Serial.println(String(gnss.getTime().hour)+":"+String(gnss.getTime().minute));

    sunTracker.setLocalisation(gnss.getCoordinates());



    sunTracker.update(sunTracker.convertDayInRank(gnss.getDate()), {gnss.getTime().hour,gnss.getTime().minute});

    for(int a=0;a<24;a++)
    {
      Serial.println(sunTracker.getElevation({a,0}));
    }

  Serial.println("#######################");
    sunTracker.update(sunTracker.convertDayInRank({21,12,24}), {gnss.getTime().hour,gnss.getTime().minute});

    for(int a=0;a<24;a++)
    {
      Serial.println(sunTracker.getElevation({a,0}));
    }

    gnss.displayInformations();

    //Serial.println(sunTracker.getAzimut());
    //Serial.println(sunTracker.getElevation());

    
    
  }
  
  // put your main code here, to run repeatedly:

//gnss.simulate();
  //gnss.readData();
  //delay(1000);
*/
}

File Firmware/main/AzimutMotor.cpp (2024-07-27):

// AzimutMotor 
#include "AzimutMotor.h"

// initialisation des paramètres
//  AzimutMotor::AzimutMotor(int enaPin, int pulsePin, int dirPin, int pas_tours, int reduction, int buteePin, float anglebutee,float angleMax) {
   // AzimutMotor(int enaPin, int pulsePin, int dirPin, int pas_tours, int reduction, int buteePin, float anglebutee,float angleMax);
AzimutMotor::AzimutMotor(uint8_t enablePin, uint8_t pulsePin, uint8_t directionPin, uint8_t endStopSensorPin)
{
  _enablePin = enablePin;
  _pulsePin = pulsePin;
  _directionPin = directionPin;
  _endStopSensorPin = endStopSensorPin;

  pinMode(this->_enablePin, OUTPUT);
  pinMode(this->_pulsePin, OUTPUT);
  pinMode(this->_directionPin, OUTPUT);
  pinMode(this->_endStopSensorPin, INPUT);


  this->_realAngle = MIN_ANGLE;
  this->_realStep = 0;

  _anglebutee = AngButee; // direction en butéee - dépend de la came- 50° est 
  _anglemax = AngMax; 
  _pas_tours = PasParTour;
  _reduction = Reduction;


  //_pasMax = (_anglemax - _anglebutee) * _pas_tours * _reduction / 360.0; // calculé : ( 310-50) * pas * reduction / 360

  this->disableDevice();
   
  
};

void AzimutMotor::enableDevice()
{
  digitalWrite(this->_enablePin, HIGH);
  this->usWait(this->_duration); 
}
void AzimutMotor::disableDevice()
{
  digitalWrite(_enablePin, LOW);
  //this->usWait(this->_duration); 
}

void AzimutMotor::usWait(uint32_t duration) 
{
  // Reset at 2^32 = 4294967296
  if (4294967295-micros() < duration) {
    while (micros() < 1000000) 
    {
      int nop = 1;
    }
  } 
  unsigned long my_micros = micros()+duration;
  while (micros() < my_micros) 
  {
    int nop = 1;
  }

}

void AzimutMotor::setDirection(bool direction)
{
  this->_direction = direction;

  digitalWrite(this->_directionPin, direction);
  this->usWait(this->_duration); 

}


bool AzimutMotor::endStopDetected()
{
  if (digitalRead(this->_endStopSensorPin) == END_STOP_DETECTED) 
  {
    this->disableDevice();
    return true;

  }
}
// privées

uint16_t AzimutMotor::setAngle(uint16_t angle)
{
  uint16_t targetAngle = angle;
  if (angle <= MIN_ANGLE) 
  { 
      targetAngle = MIN_ANGLE;
  }
  else if ( angle >= MAX_ANGLE ) {
      targetAngle = MAX_ANGLE;
  }
  else {
   
  }

  // calcul du nombre de steps du moteur
  int16_t steps_A = int(targetAngle - this->_realAngle) * STEP_PER_TOUR ;
  uint16_t stepTarget = int(float(steps_A) /360.0) * MECHANICAL_GEAR_RATIO;

  this->enableDevice();
  if (stepTarget < 0) 
  {
    this->makeSteps(abs(stepTarget), DIRECTION_WEST);
    this->_realAngle = targetAngle;
    this->_realStep += abs(stepTarget);
  }
  else 
  {
    this->makeSteps(abs(stepTarget), DIRECTION_EST);
    this->_realAngle = targetAngle;
    this->_realStep += abs(stepTarget);
  }
  this->disableDevice();
    /**/
    return stepTarget;
}


void AzimutMotor::makeStep()
{
    digitalWrite(this->_pulsePin, HIGH);
    this->usWait(this->_duration);
    digitalWrite(this->_pulsePin, LOW);
    this->usWait(this->_duration);
}

int AzimutMotor::makeSteps(uint32_t steps, bool direction) 
{
  uint32_t stepDone=0;
  // Set the spinning direction clockwise:

  this->enableDevice();
  this->usWait(this->_duration); 

  this->setDirection(direction);
  this->usWait(this->_duration); 
  
   for (int i = 0; i < steps; i++) {

   /* if(this->endStopDetected() == true) 
    {
      break;
    }*/
    this->makeStep();
    stepDone += 1;
   
  }
   this->disableDevice();
   return stepDone;
}



int AzimutMotor::returnToEst()
{

  uint8_t endStopValue = digitalRead(this->_endStopSensorPin);

  if (endStopValue == END_STOP_NO_DETECTED) 
  {
    
    this->setDirection(DIRECTION_EST);
    this->enableDevice();

    while (digitalRead(this->_endStopSensorPin) != END_STOP_DETECTED) 
    {
      this->makeStep();
    }
    
    this->setDirection(DIRECTION_WEST);

    while (digitalRead(this->_endStopSensorPin) == END_STOP_DETECTED) 
    {
      this->makeStep();
    }

    this->disableDevice();
  }
  else 
  {
    this->setDirection(DIRECTION_WEST);
    this->enableDevice();

    while (digitalRead(this->_endStopSensorPin) == END_STOP_DETECTED) 
    {
      this->makeStep();
    }
    this->disableDevice();

  }//End else

  this->disableDevice();
  this->_realAngle = MIN_ANGLE;
  //_pascourant = 0;

  return 0;
};



int AzimutMotor::returnToWest()
{

    uint8_t endStopValue = digitalRead(this->_endStopSensorPin);

  if (endStopValue == END_STOP_NO_DETECTED) 
  {
    
    this->setDirection(DIRECTION_WEST);
    this->enableDevice();

    while (digitalRead(this->_endStopSensorPin) != END_STOP_DETECTED) 
    {
      this->makeStep();
    }
    
    this->setDirection(DIRECTION_EST);

    while (digitalRead(this->_endStopSensorPin) == END_STOP_DETECTED) 
    {
      this->makeStep();
    }

    this->disableDevice();
  }
  else 
  {
    this->setDirection(DIRECTION_EST);
    this->enableDevice();

    while (digitalRead(this->_endStopSensorPin) == END_STOP_DETECTED) 
    {
      this->makeStep();
    }
    this->disableDevice();

  }//End else

  this->disableDevice();
  this->_realAngle = MIN_ANGLE;
  this->_realStep = 0;

  return 0;
};

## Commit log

2023-08-27 Add PCB
    [Tracker.kicad_pcb, Tracker.kicad_sch]
2023-08-29 Add first code
    [SUN.kicad_sch, Tracker.kicad_pcb, Tracker.kicad_sch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]
2023-09-22 Add PCB with GNSS
    [132255.stp, 8967560.stp, AVR_ISP_2R5W_254P.STEP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]
2023-11-29 Update of repository
    [132255.stp, 8967560.stp, AVR_ISP_2R5W_254P.STEP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]
2024-01-22 update of directory
    [GNSS.kicad_sch, Motors.kicad_sch, Tracker.kicad_pcb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]
2024-03-06 Update of PCB
    [GNSS.kicad_sch, Motors.kicad_sch, Tracker.kicad_pcb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]
2024-03-17 Update PCB of Motor controller - version sent on production (debug purpose)
    [GNSS.kicad_sch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]
2024-05-28 Add CMS version
    [132255.stp, 8967560.stp, AVR_ISP_2R5W_254P.STEP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]
2024-09-15 Update 4Layers
    [GNSS.kicad_sch]

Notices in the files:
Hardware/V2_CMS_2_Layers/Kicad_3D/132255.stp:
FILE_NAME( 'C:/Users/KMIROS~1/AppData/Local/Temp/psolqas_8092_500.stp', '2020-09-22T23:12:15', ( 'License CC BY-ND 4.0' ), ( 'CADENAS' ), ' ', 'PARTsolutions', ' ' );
